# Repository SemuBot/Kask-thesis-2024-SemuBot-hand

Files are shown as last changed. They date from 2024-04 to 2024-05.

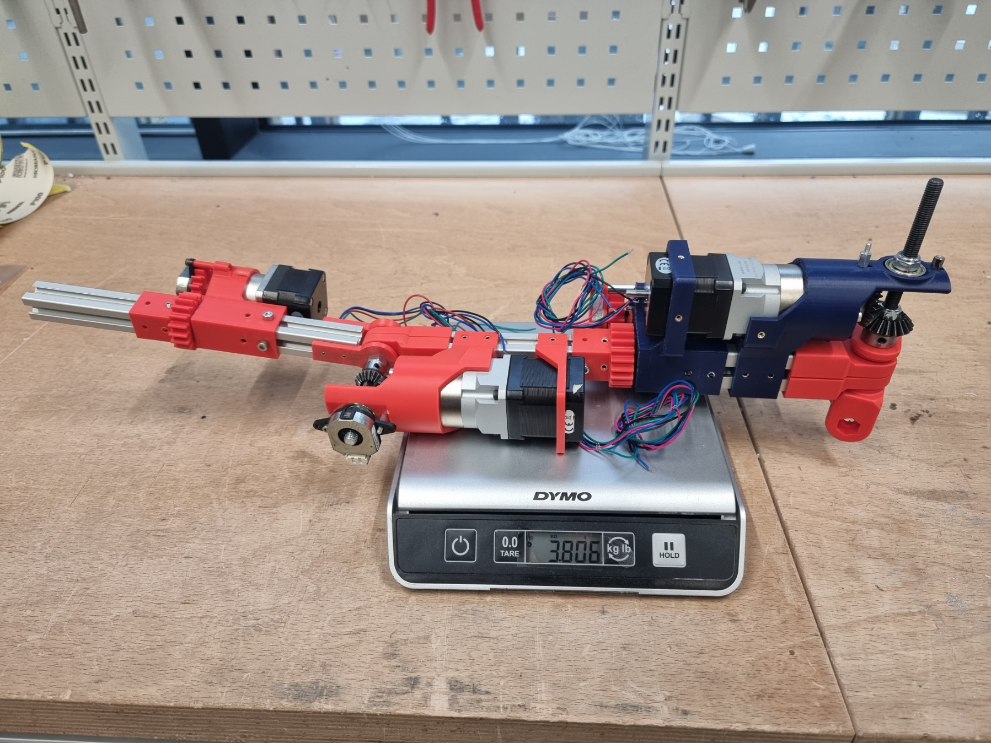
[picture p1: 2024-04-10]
Pictures/Complete parts separately/SB_hand_on_scale.jpg

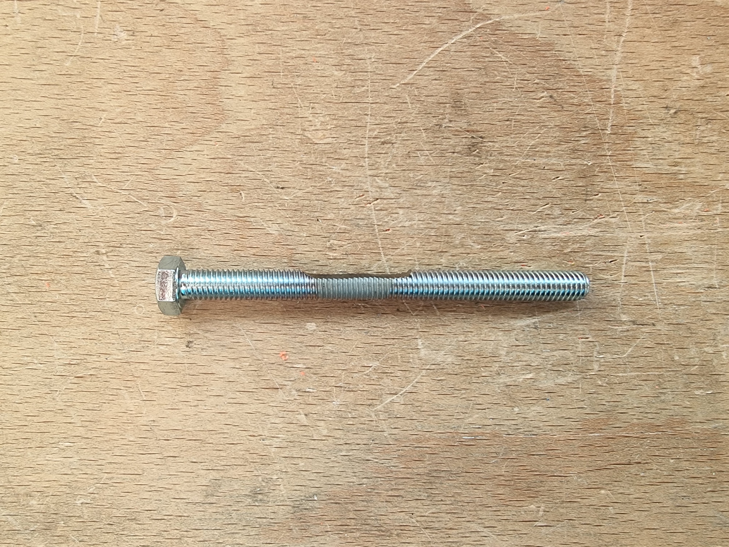
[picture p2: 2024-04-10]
Pictures/Not 3D-printed parts/Filed_M8_bolt_elbow.jpg

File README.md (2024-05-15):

# SemuBot hand from shoulder to wrist
Author: Kristjan Madis Kask

## ENG
Welcome to the repository of SemuBot hand design materials. By clicking on the link below, you can see the composition of two hands on Fusion website. From the folders, you can view design STL and 3D-printing 3mf files, pictures and videos, and some failed solutions are alse on the pictures. 

## EST
Tere Tulemast SemuBoti käe disainimaterjalide hoidlasse. Allpool on võimalik lingile klikates näha kahe käe koostu Fusioni veebilehel. Kaustadest saab näha disaini STL ja printimise 3mf faile, pilte ja videoid ning välja on toodud piltidel ka kehvad ja ebaõnnestunud lahendused. 

## Assembly with two hands in Fusion 360
https://a360.co/3OWJDU3

## One hand movement gif


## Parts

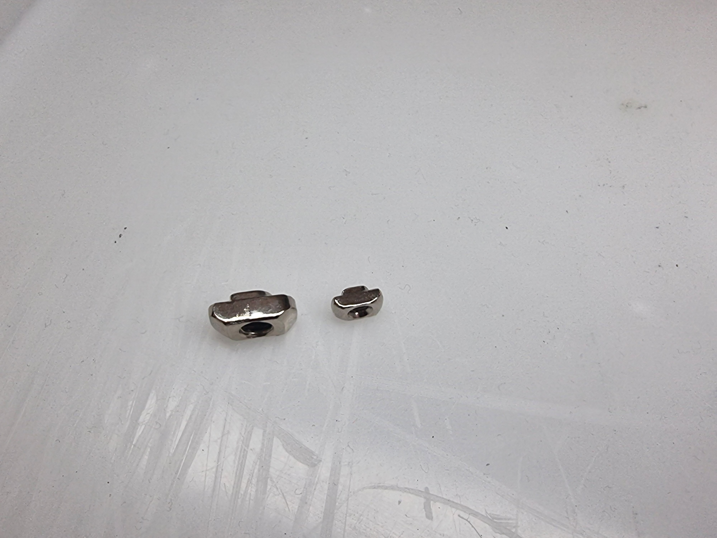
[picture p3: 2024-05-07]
Pictures/Not 3D-printed parts/30mm&20mm_alu_extrusion_fixers.jpg

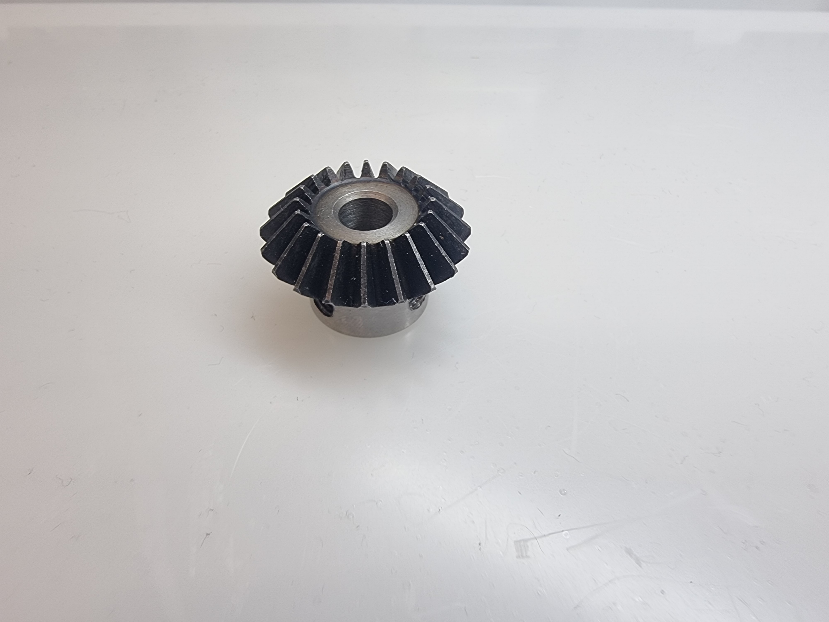
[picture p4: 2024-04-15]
Pictures/Not 3D-printed parts/Bevel_gear_bigger.jpg

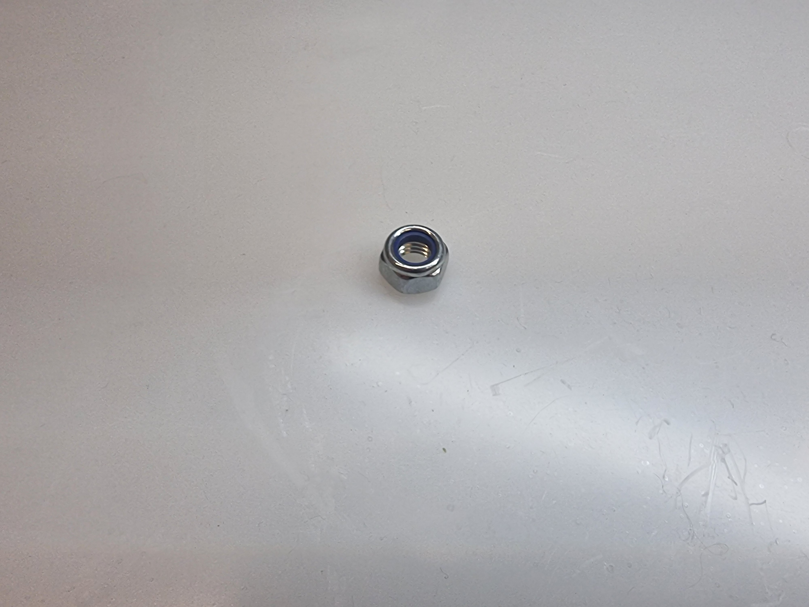
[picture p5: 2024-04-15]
Pictures/Not 3D-printed parts/M8_nylock_nut.jpg

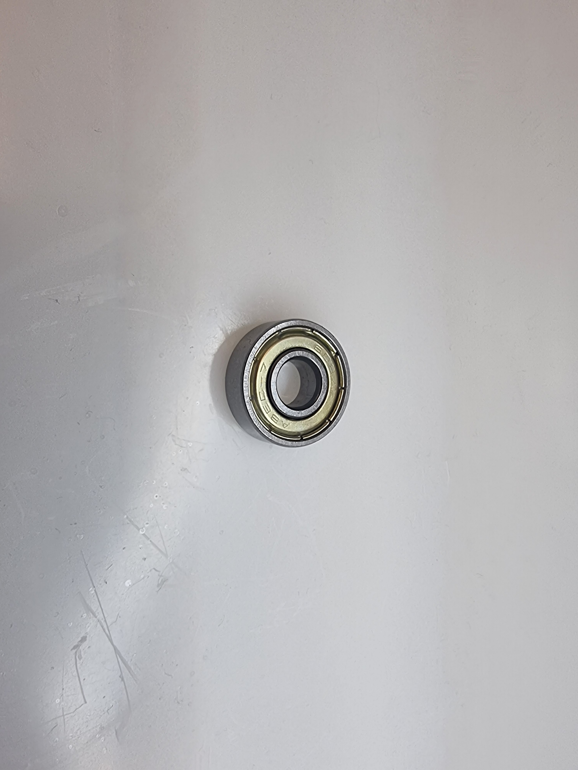
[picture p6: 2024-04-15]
Pictures/Not 3D-printed parts/Bearing.jpg

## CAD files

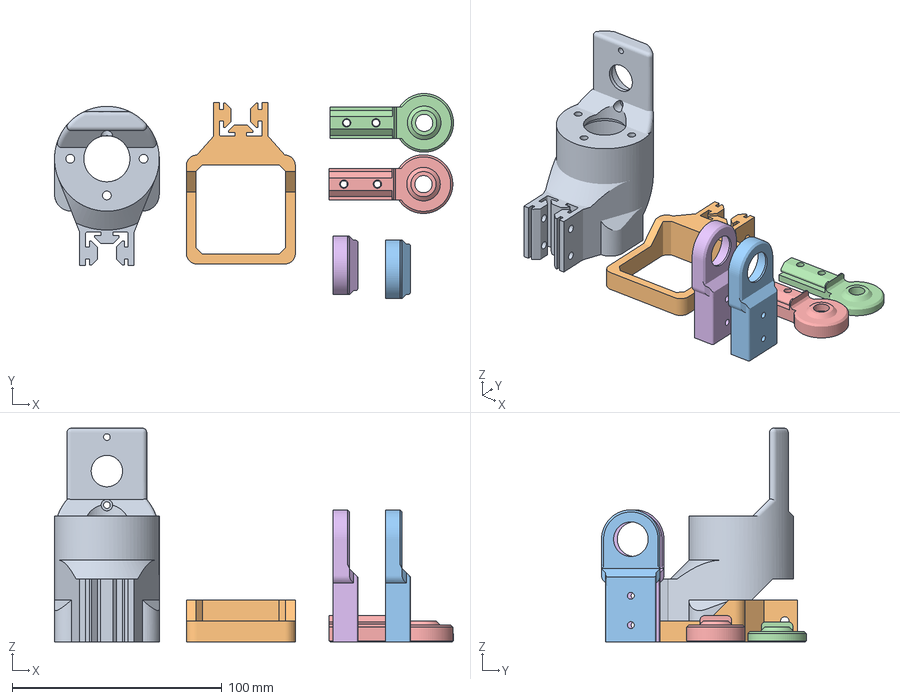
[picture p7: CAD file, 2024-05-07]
Design/3mf print files/Bambu prints/SB_elbow_set.3mf
190.4 x 97.8 x 102.0 mm
SB_elbow_Nema17&gearbox_mount.stl
SB_elbow_Nema17_mount.stl
SB_elbow_w_bearings.stl x 2
SB_elbow_wo_bearings.stl
SB_elbow_wo_bearings_w_hex.stl

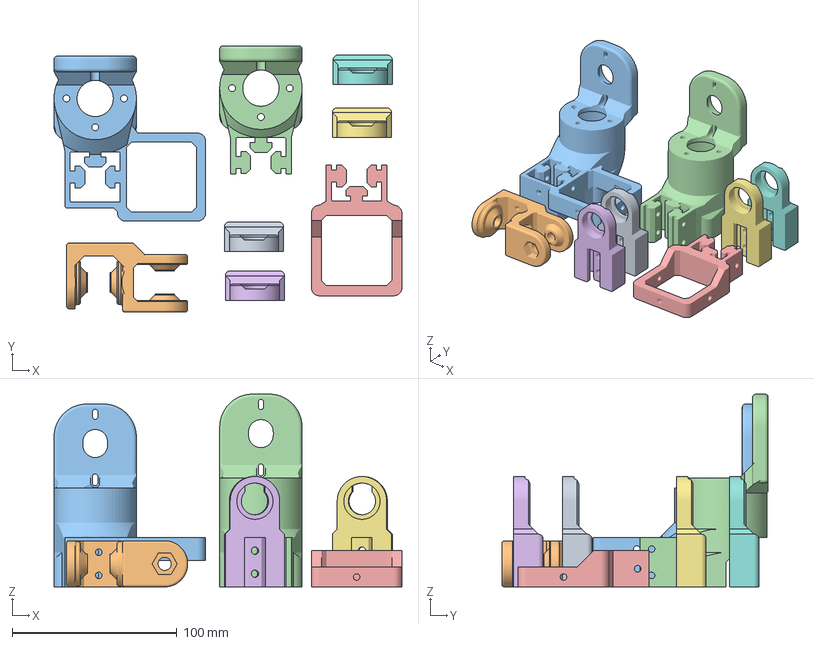
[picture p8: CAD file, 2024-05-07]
Design/3mf print files/Prusa prints/SB_right_shoulder_set.3mf
211.1 x 161.6 x 117.0 mm
SB_shoulder_mount_w_bearings.stl x 4
SB_shoulder_mount_wo_bearings.stl
SB_shoulder_right_upper_arm_Nema17&gearbox_mount.stl
SB_shoulder_shoulder_Nema17&gearbox_mount.stl
SB_shoulder_shoulder_Nema17_mount.stl

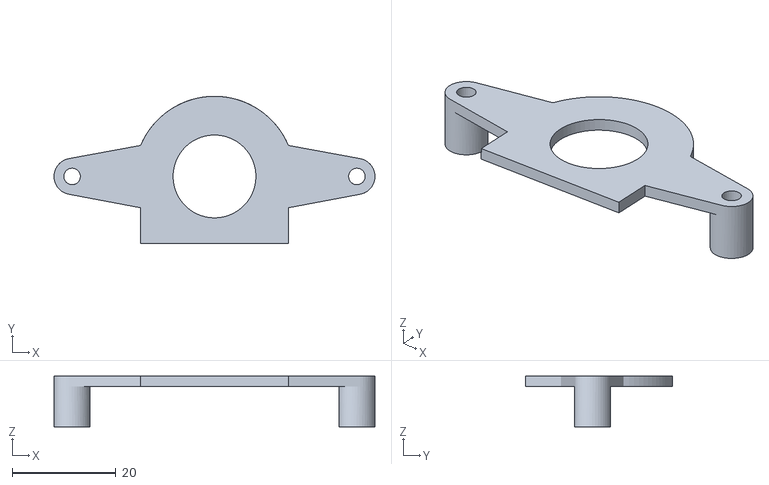
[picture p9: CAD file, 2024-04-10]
Design/STL files/Arm/SB_arm_turn_encoder_mount_top.stl
62.0 x 28.5 x 9.80

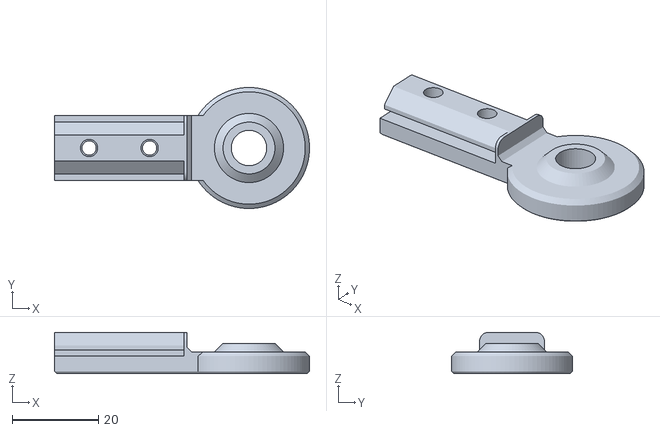
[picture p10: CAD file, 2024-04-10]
Design/STL files/Elbow/SB_elbow_wo_bearings.stl
59.0 x 28.0 x 9.50

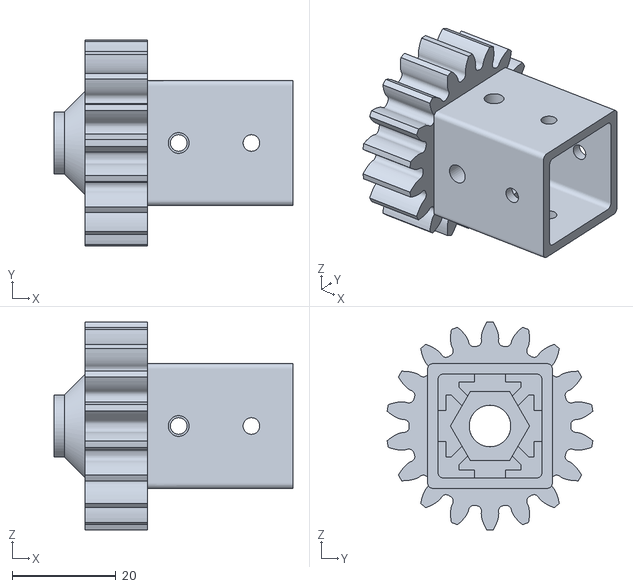
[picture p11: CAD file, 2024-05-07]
Design/STL files/Forearm/SB_forearm_turn_wo_bearings.stl
46.0 x 39.6 x 40.0

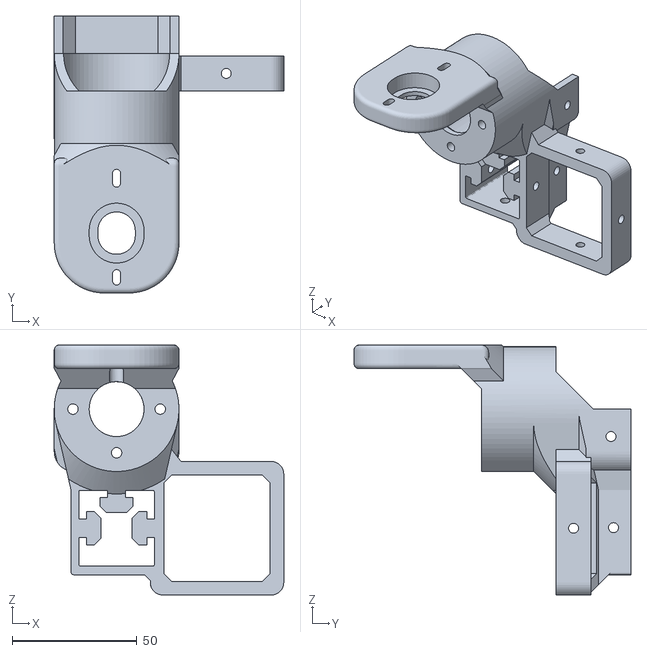
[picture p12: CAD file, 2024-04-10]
Design/STL files/Shoulder/SB_shoulder_right_upper_arm_Nema17&gearbox_mount.stl
92.0 x 111.0 x 100.2

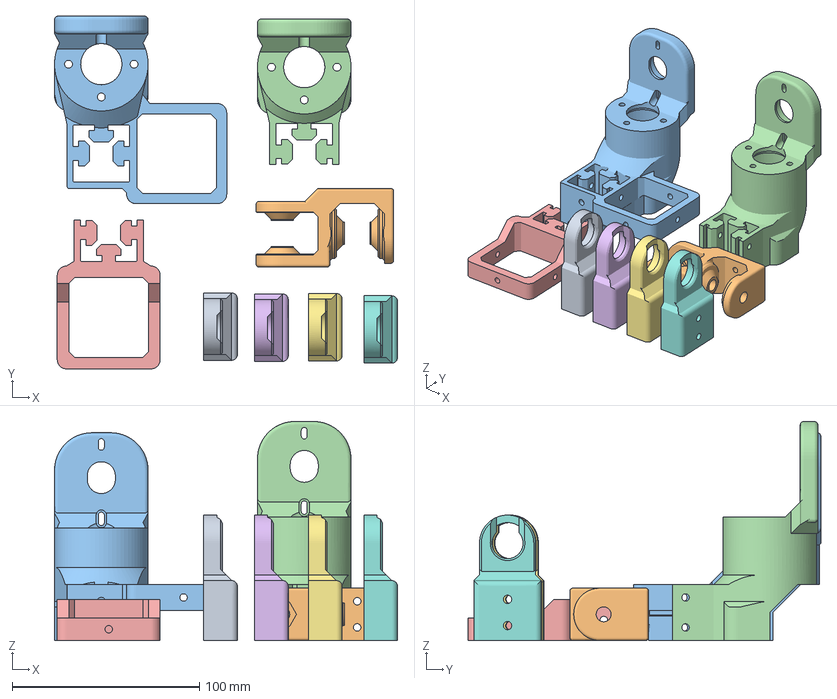
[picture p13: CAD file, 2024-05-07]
Design/3mf print files/Bambu prints/SB_right_shoulder_set.3mf
183.2 x 188.4 x 117.0 mm
SB_shoulder_mount_w_bearings.stl x 4
SB_shoulder_mount_wo_bearings.stl
SB_shoulder_right_upper_arm_Nema17&gearbox_mount.stl
SB_shoulder_shoulder_Nema17&gearbox_mount.stl
SB_shoulder_shoulder_Nema17_mount.stl

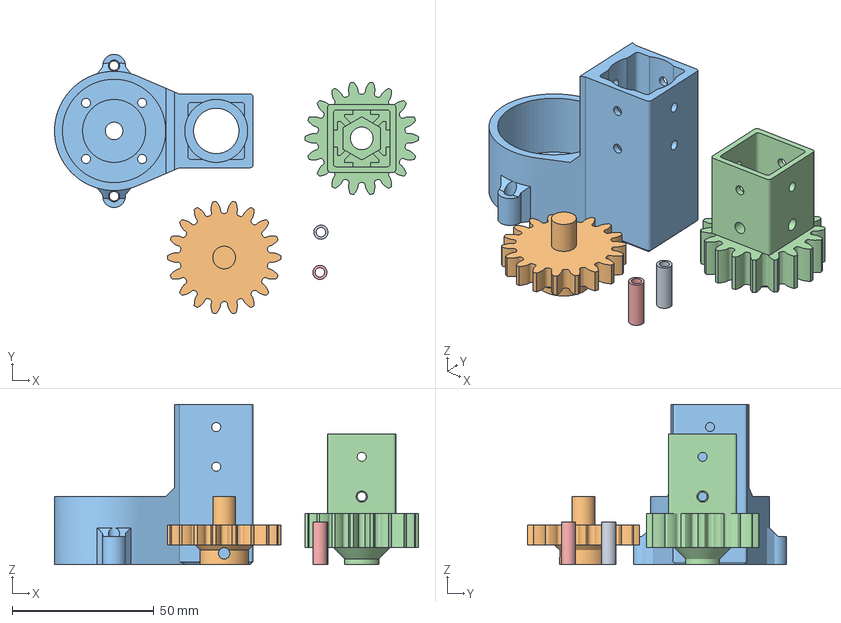
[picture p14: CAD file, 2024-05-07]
Design/3mf print files/Prusa prints/SB_forearm_turn_set.3mf
128.3 x 91.4 x 56.5 mm
SB_forearm_turn_encoder_washer.stl x 2
SB_forearm_turn_stepper_gear.stl
SB_forearm_turn_w_bearings.stl
SB_forearm_turn_wo_bearings.stl

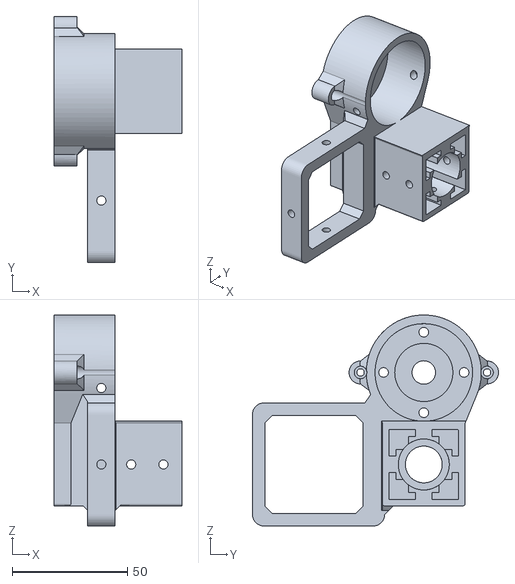
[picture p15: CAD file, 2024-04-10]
Design/STL files/Arm/SB_arm_turn_w_bearings_right.stl
55.5 x 107.0 x 91.7

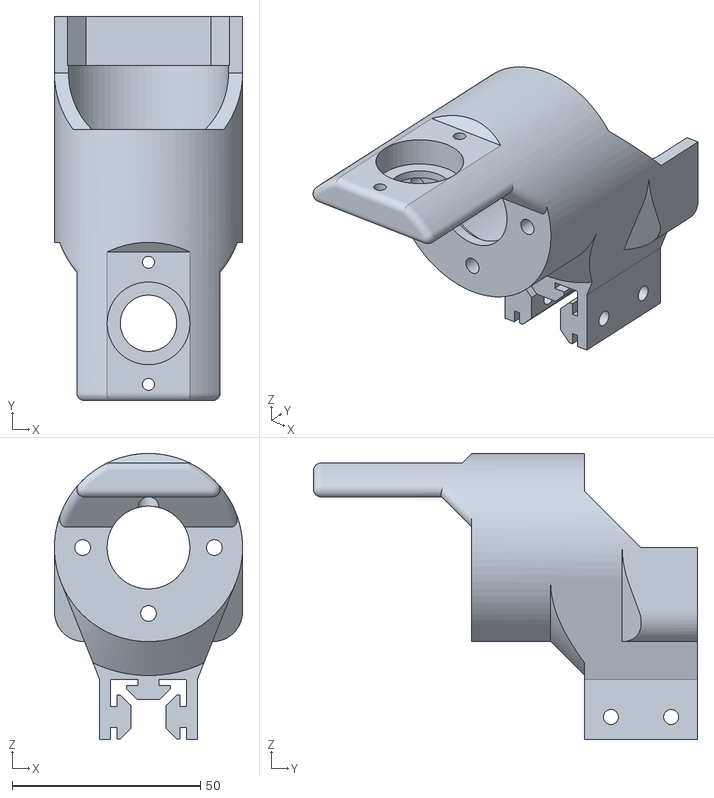
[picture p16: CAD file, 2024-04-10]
Design/STL files/Elbow/SB_elbow_Nema17&gearbox_mount.stl
50.0 x 102.0 x 76.0

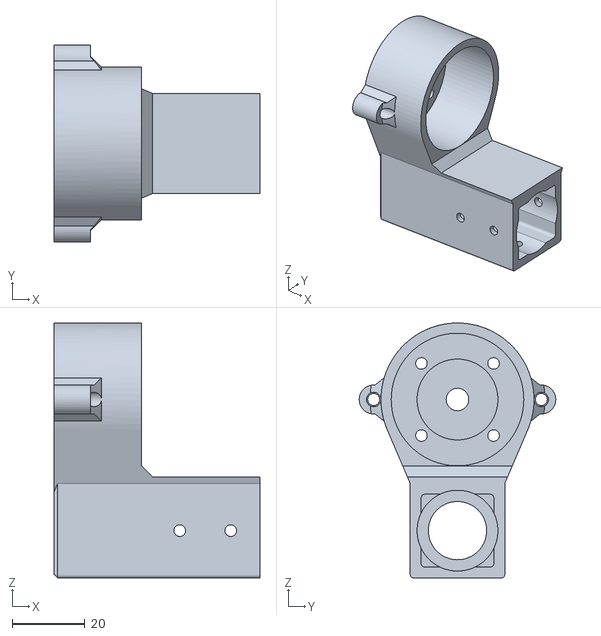
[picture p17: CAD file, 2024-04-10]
Design/STL files/Forearm/SB_forearm_turn_w_bearings.stl
56.5 x 54.0 x 70.0

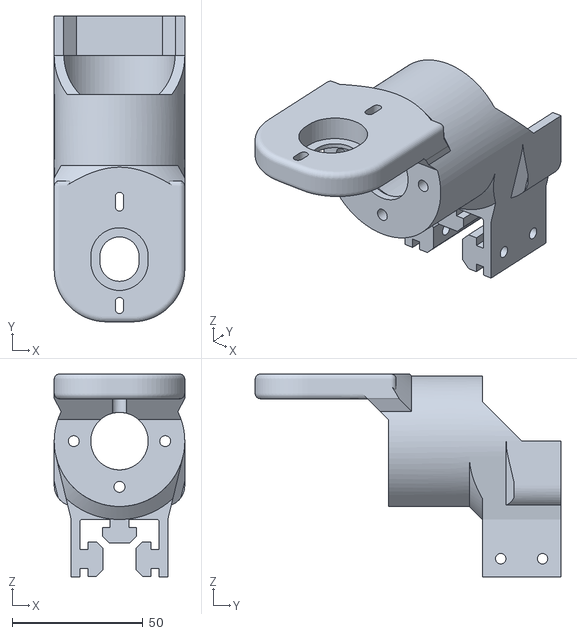
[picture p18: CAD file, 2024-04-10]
Design/STL files/Shoulder/SB_shoulder_shoulder_Nema17&gearbox_mount.stl
50.0 x 117.0 x 77.7

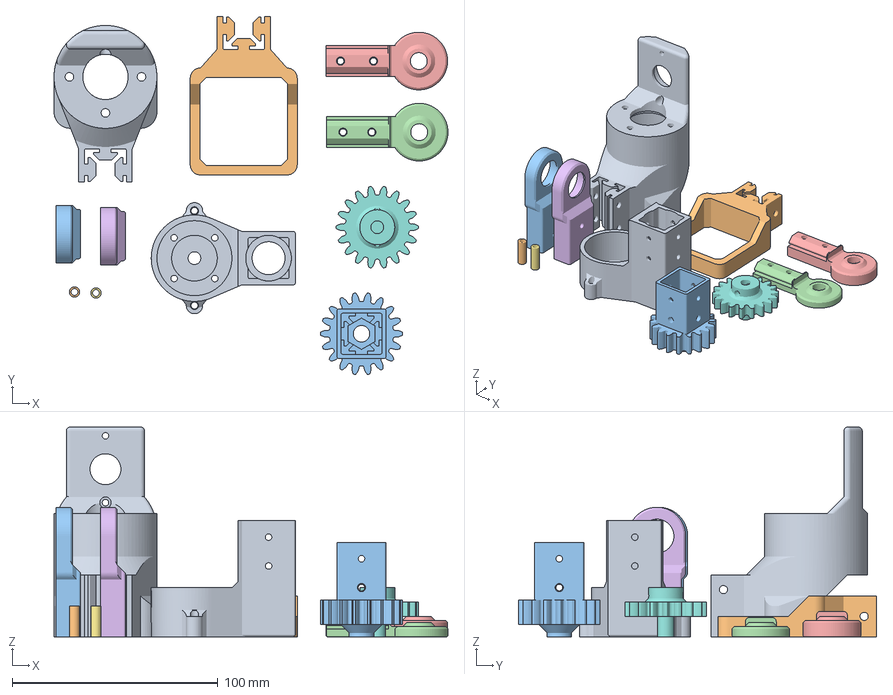
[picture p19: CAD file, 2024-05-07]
Design/3mf print files/Bambu prints/SB_elbow&forearm_set.3mf
191.4 x 173.9 x 102.0 mm
SB_elbow_Nema17&gearbox_mount.stl
SB_elbow_Nema17_mount.stl
SB_elbow_w_bearings.stl x 2
SB_elbow_wo_bearings.stl
SB_elbow_wo_bearings_w_hex.stl
SB_forearm_turn_encoder_washer.stl x 2
SB_forearm_turn_stepper_gear.stl
SB_forearm_turn_w_bearings.stl
SB_forearm_turn_wo_bearings.stl

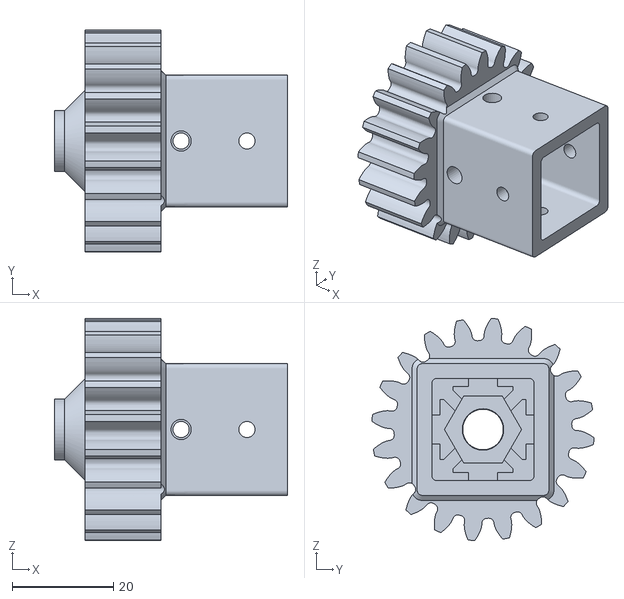
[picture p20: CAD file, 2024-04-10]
Design/STL files/Arm/SB_arm_turn_wo_bearings.stl
46.0 x 43.9 x 43.9

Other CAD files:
Design/3mf print files/Prusa prints/SB_elbow&forearm_set.3mf
Design/STL files/Elbow/SB_elbow_Nema17_mount.stl
Design/STL files/Shoulder/SB_shoulder_left_upper_arm_Nema17&gearbox_mount.stl
Design/3mf print files/Bambu prints/SB_right_arm_set.3mf
Design/3mf print files/Bambu prints/SB_forearm_turn_set.3mf
Design/3mf print files/Prusa prints/SB_elbow_set.3mf
Design/3mf print files/Prusa prints/SB_right_arm_set.3mf
Design/STL files/Arm/SB_arm_turn_encoder_mount.stl
Design/STL files/Arm/SB_arm_turn_stepper_gear.stl
Design/STL files/Arm/SB_arm_turn_w_bearings_left.stl
Design/STL files/Elbow/SB_elbow_w_bearings.stl
Design/STL files/Elbow/SB_elbow_wo_bearings_w_hex.stl
Design/STL files/Forearm/SB_forearm_turn_encoder_washer.stl
Design/STL files/Forearm/SB_forearm_turn_stepper_gear.stl
Design/STL files/Shoulder/SB_shoulder_mount_w_bearings.stl
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

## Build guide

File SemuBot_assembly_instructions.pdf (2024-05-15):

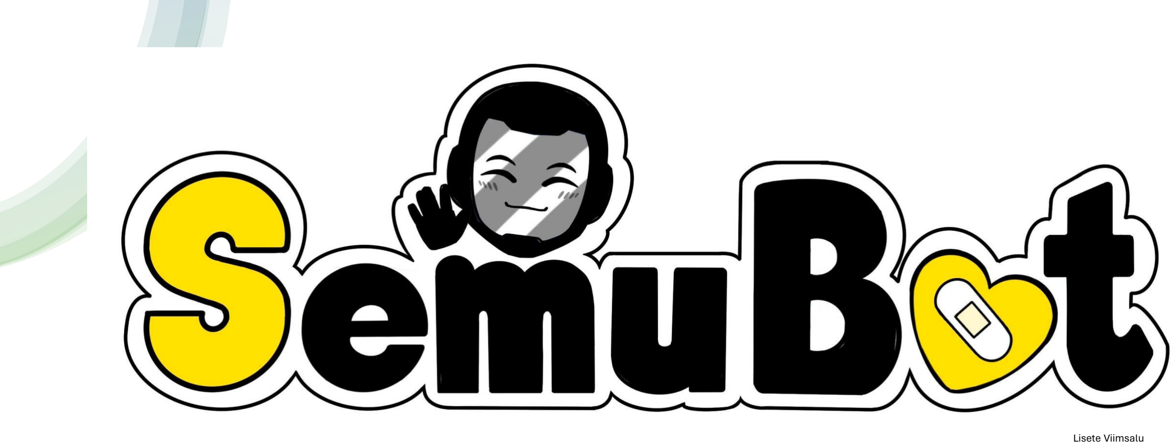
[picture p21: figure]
Lisete Viimsalu
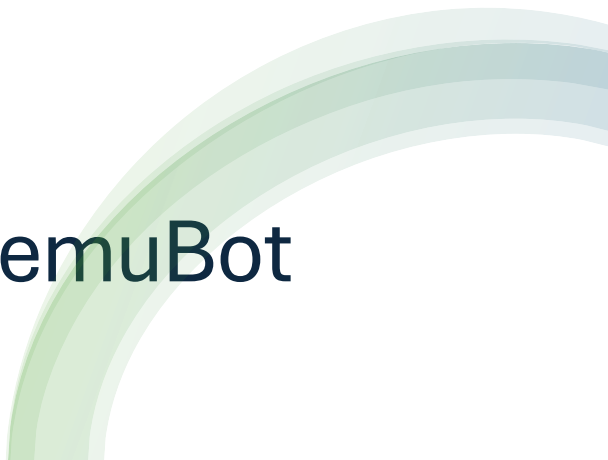
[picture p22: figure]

## Arm mechanics assembly instructions for SemuBot

Kristjan Madis Kask

## Final solution and parts separately

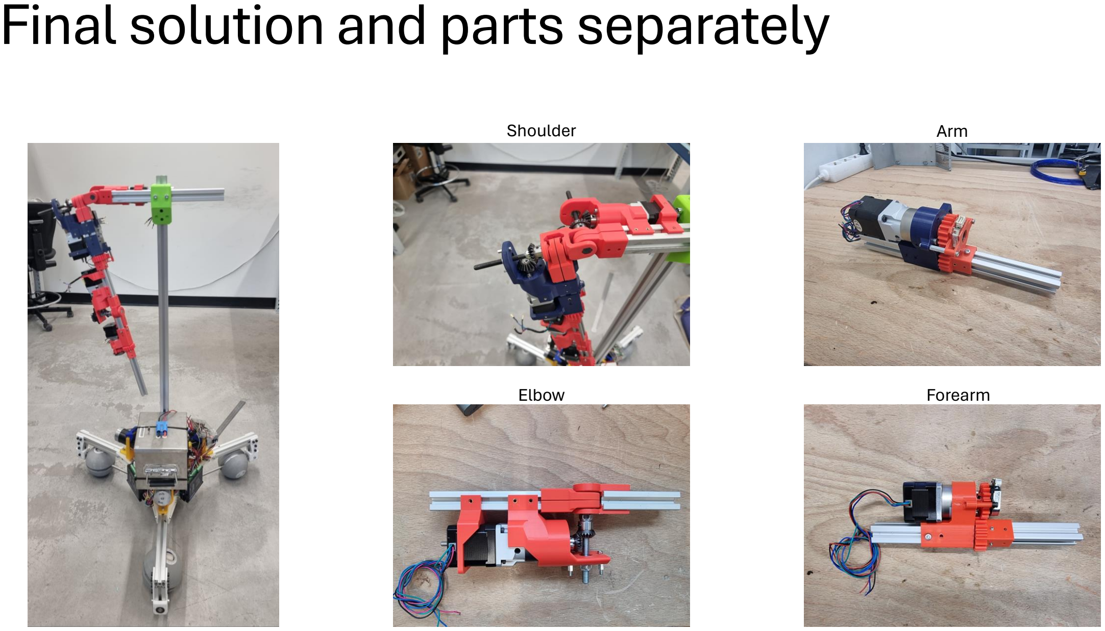
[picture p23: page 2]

Shoulder | Arm
Elbow | Forearm

# Required mechanical parts

Detail | Amount | Picture
30x30 and 20x20 aluminium extrusions | 2x Extrusion30x30 3x Extrusion20x20
M3 and M4 bolts | 22x M3 bolts 12X M4 bolts
M8 bolt | 3
M8 nylock nut | 6
M3 set screw | 44
M3 long nut | 8
30x30 and 20x20 extrusion mounts | 4x mounts for 30x30 7x mounts for 20x20

# Required mechanical parts

Detail | Amount | Picture
Threaded insert | 44
Bearing 608zz 8x22x7 | 13
Smaller 45° bevel gear with 20 teeth | 2

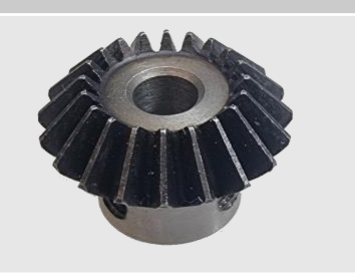
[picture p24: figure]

Bigger 45° bevel gear with 20 teeth | 4

## Forearm

1. 3D-print details from forearm folder (mount with bearings, mount without bearings, gear for motor and 2 encoder washers)
2. Melt threaded inserts in place and add set screws (4 sets for mount without bearings, 2 sets for motor bearing and 2 inserts for mount with bearings to attach encoder)
3. Add bearings to mount with bearings (blue one on the next page) and fix the parts with a M8 bolt and nylock nut
4. Put 20x20 extrusion mounts and M4 bolts in place and attach parts to extrusions
5. Fix stepper motor with M3 bolts and motor bearing with set screws
6. Use M3 bolts and 3D-printed washers to screw encoder in place

## Forearm

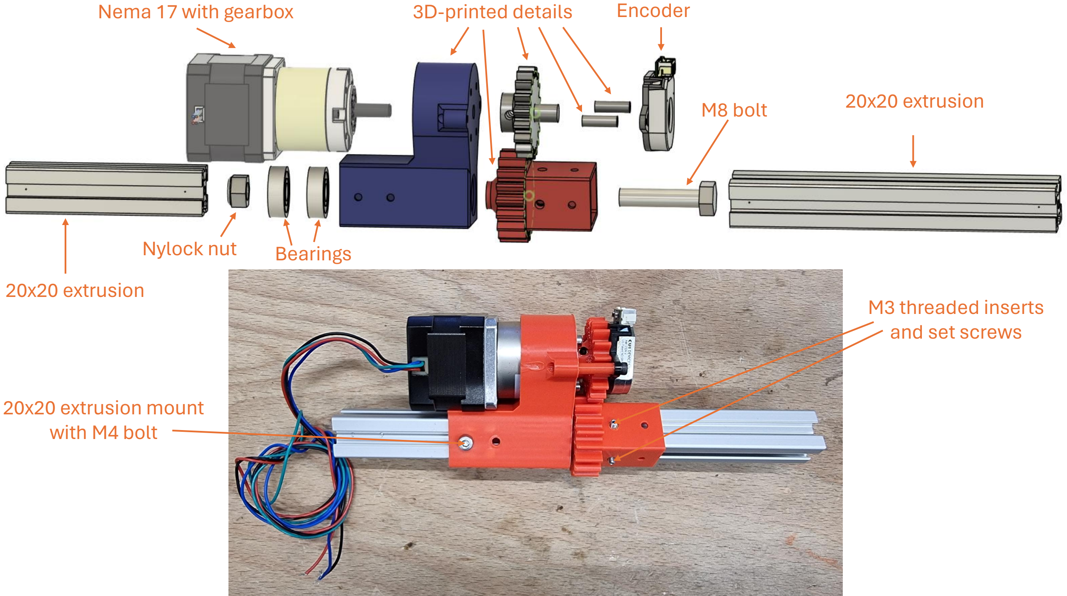
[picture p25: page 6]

Nema 17 with gearbox | Encoder

M8 bolt

Nylock nut Bearings

20x20 extrusion

20x20 extrusion

3D-printed details

M3 threaded inserts
and set screws

20x20 extrusion mount
with M4 bolt

## Elbow

1. 3D-print details from elbow folder (motor mounts, elbow mounts without bearings and elbow mounts with bearings)
2. Melt threaded inserts in place and add set screws (6 sets for motor mounts and 4 sets for elbow mounts)
3. Put M3 bolts and long M3 nuts in place for encoder
4. Add bearings to elbow mounts and fix the parts in place on the 20x20 extrusions
5. Abrade M8 bolt as shown in the picture on the nex slide
6. Slide the motor mounts on the extrusion and put M8 bolt, nyloc nut, bevel gear and outer bearing and nylock nut in place
7. When 1st nylock nut and bevel gear are tightened, add motor with gearbox and bevel gear attached to it
8. Attach outer nyloc nut and encoder

## Abraded M8 bolt for elbow

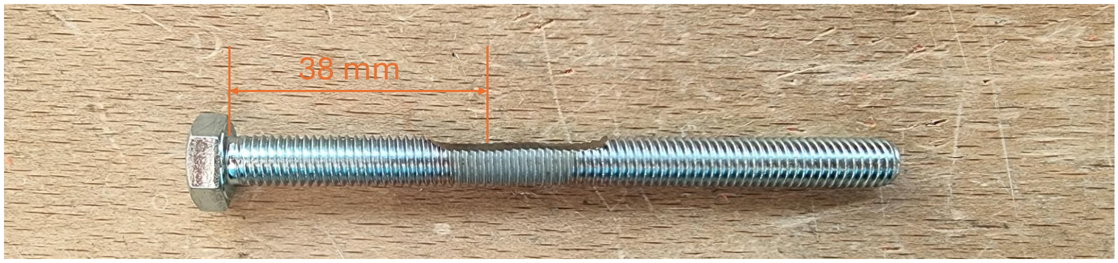
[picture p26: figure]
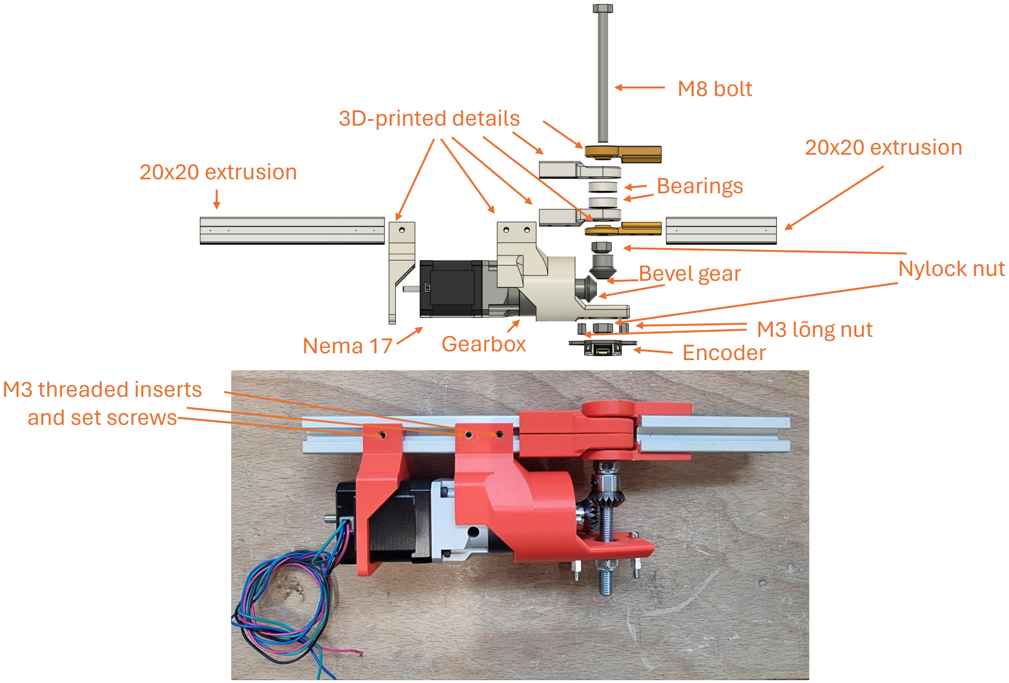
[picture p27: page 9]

20x20 extrusion

20x20 extrusion

3D-printed details

Nema 17 Gearbox

Bearings

Nylock nut

Encoder

M3 lõng nut

Bevel gear

M8 bolt

M3 threaded inserts
and set screws

## Arm

1. 3D-print details from arm folder (mount with bearings, mount without bearings, gear for motor and encoder top and bottom mounts)
2. Melt threaded inserts in place and add set screws (6 sets for mount without bearings and 2 sets for motor gear)
3. Add bearings to mount with bearings (blue one on the next page) and fix the parts with a M8 bolt and nylock nut
4. Put 20x20 extrusion mounts and M4 bolts in place and attach parts to extrusions
5. Fix stepper motor to gearbox and with M4 bolts attach it to the mount
6. Attach 3D-printed parts in place
7. Use M3 bolts, long nuts and printed encoder mounts to screw encoder in place

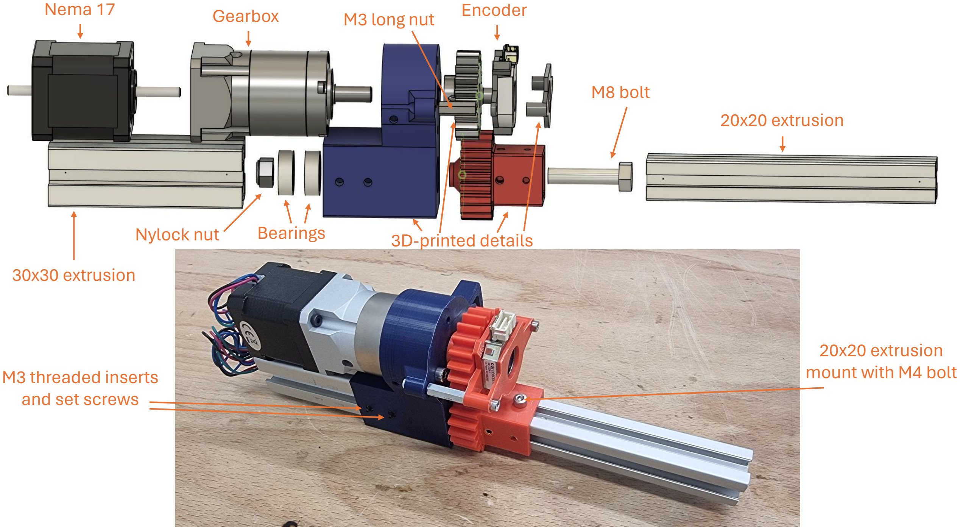
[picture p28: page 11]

Nema 17 | Gearbox | Encoder

M8 bolt

Nylock nut Bearings

20x20 extrusion

30x30 extrusion

3D-printed details

M3 long nut

M3 threaded inserts
and set screws

20x20 extrusion
mount with M4 bolt

## Shoulder

1. 3D-print details from shoulder folder (motor mounts, shoulder mounts with and without bearings, and shoulder-spine mount if needed)
2. Melt threaded inserts in place and add set screws (18 sets for motor mounts and 4 sets for shoulder mounts)
3. Put M3 bolts and long M3 nuts in place for encoder
4. Add bearings to shoulder mounts and fix the parts in place on the 30x30 extrusions
5. Abrade M8 bolt as shown in the picture on the nex slide
6. First you have to attach the upper arm motor (blue one in the picture) and secondly the shoulder one
7. Slide the motor mounts on the extrusions and put M8 bolt, nyloc nut, bevel gear and outer bearing and nylock nut in place
8. Attach motors to motor mounts with M4 bolts and then add bevel gears as well
9. When motor with gearbox is fixed to the mount, slide it in place on the extrusion and start screwing the bolt and nut
10. When 1st nylock nut and bevel gear are tightened, fix the outer bearing with a nylock nut. Repeat the process for other motor
11. Attach encoders

## Abraded M8 bolt for shoulder

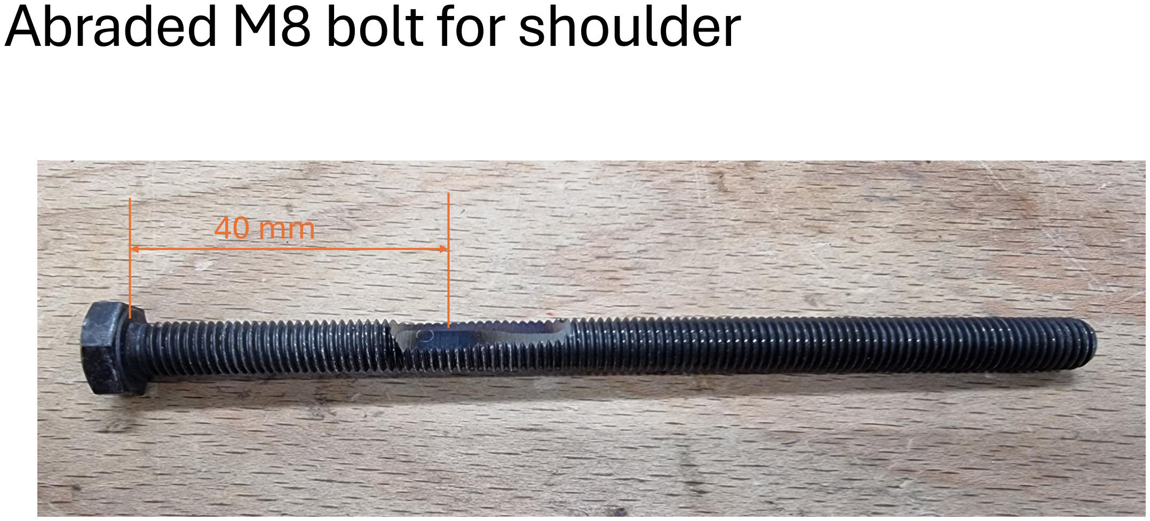
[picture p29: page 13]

40 mm

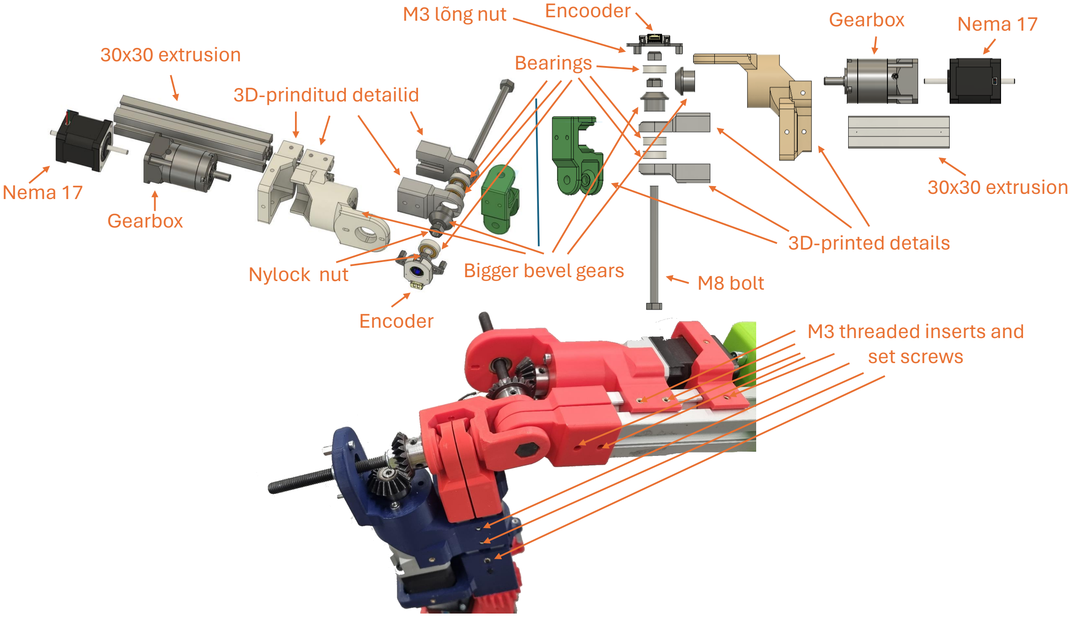
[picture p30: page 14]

Nema 17
Gearbox

Encooder

M8 bolt

Bearings

Nylock nut

30x30 extrusion

30x30 extrusion

3D-printed details

M3 lõng nut | Gearbox | Nema 17

3D-prinditud detailid

Encoder

Bigger bevel gears

M3 threaded inserts and
set screws

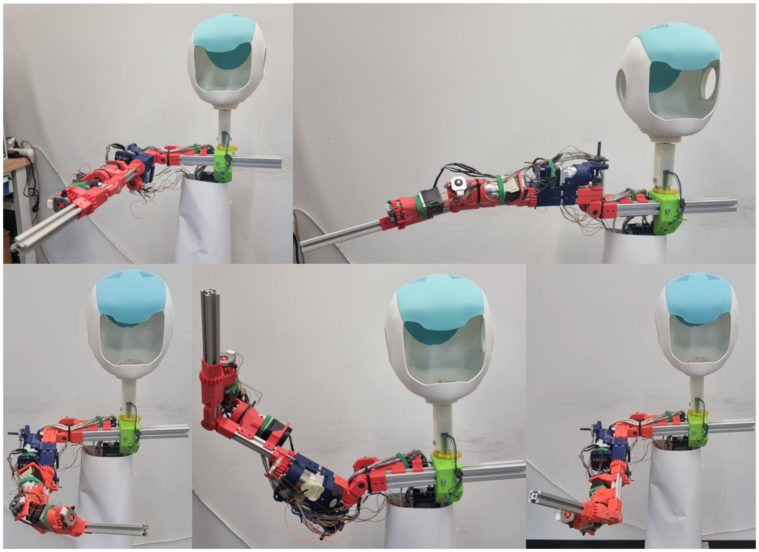
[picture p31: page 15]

## Arm mechanics assembly instructions for SemuBot

Kristjan Madis Kask

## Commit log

2024-04-10 Added .stl models
    [SB_arm_encoder_mount_set.3mf, SB_arm_turn_encoder_mount.stl, SB_arm_turn_encoder_mount_top.stl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]
2024-04-15 Added pictures of not 3D-printed parts
2024-04-17 Changed folder names
    [SB_arm_encoder_mount_set.3mf, SB_arm_turn_encoder_mount.stl, SB_arm_turn_encoder_mount_top.stl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]
2024-04-17 Folder corrections
    [SB_arm_encoder_mount_set.3mf, SB_arm_turn_encoder_mount.stl, SB_arm_turn_encoder_mount_top.stl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]
2024-05-07 Added printing files
    [SB_arm_encoder_mount_set.3mf, SB_elbow&forearm_set.3mf, SB_elbow_set.3mf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]
